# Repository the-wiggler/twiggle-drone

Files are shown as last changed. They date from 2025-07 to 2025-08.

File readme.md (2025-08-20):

## Twiggle Drone Project
An from-scratch quadcopter built using Arduino, and capable of stable flight controlled via a WiFi connection. 

---

## Features
- Built with **Arduino Nano ESP32**
- 4x Brushless motors with PWM control
- ICM20948 for attitude sensing
- Custom PID stabilization program
- Manual flight via a GUI computer program (UDP over WiFi)

## Components
| Component | Description | Quantity | Link |
|---|---|---|---|
| Arduino Nano ESP32 | Main microcontroller | 1 | [Link](https://www.digikey.com/en/products/detail/arduino/ABX00092/21219771) |
| Adafruit ICM20948 | Gyroscope + Accelerometer | 1 | [Link](https://www.digikey.com/en/products/detail/adafruit-industries-llc/4554/17039173) |
| Adafruit Powerboost 1000 | 3.7V → 5V power converter | 1 | [Link](https://www.digikey.com/en/products/detail/adafruit-industries-llc/2030/5011076) |
| Adafruit USB C Breakout | Provide power to Arduino USB C port | 1 | [Link](https://www.digikey.com/en/products/detail/adafruit-industries-llc/5978/24639123) |
| N-Channel MOSFET | Used for PWM motor control | 4 | [Link](https://www.digikey.com/en/products/detail/infineon-technologies/IRLZ44NPBF/811808) |
| 8520 Coreless Brushed Motors | Drone motors/rotors | 4 | [Link](https://www.amazon.com/dp/B076M7G24G?ref=ppx_yo2ov_dt_b_fed_asin_title) |
| GNB 3.8V 520mAh LiPo Battery (80C) | Battery | 1 | [Link](https://www.amazon.com/dp/B07QC17GLT?ref=ppx_yo2ov_dt_b_fed_asin_title) |
| Drone Body | 3D printed body | 1 | [link](about:blank) |

## Project Structure
twiggle-drone/<br>
├── src/<br>
│   ├── main.cpp<br>
│   └── // arduino files (to be uploaded to arduino)<br>
├── controller/<br>
│   ├── main.cpp<br>
│   └── // controller files (to be run on local machine)<br>

## Getting Started
1. **Construct the drone**
    - The drone is activated when it receives battery power, and will wait for controller input via UDP over wifi
2. **Run the controller program**
    - build the controller program found in /controller/
    - this program should be run on a computer with the ability to connect to WiFi networks
    - connect to the drone's WiFi network before running the program
    - run the program, and the drones motors should begin at an idle state. The drone is ready to fly
### Schematic:
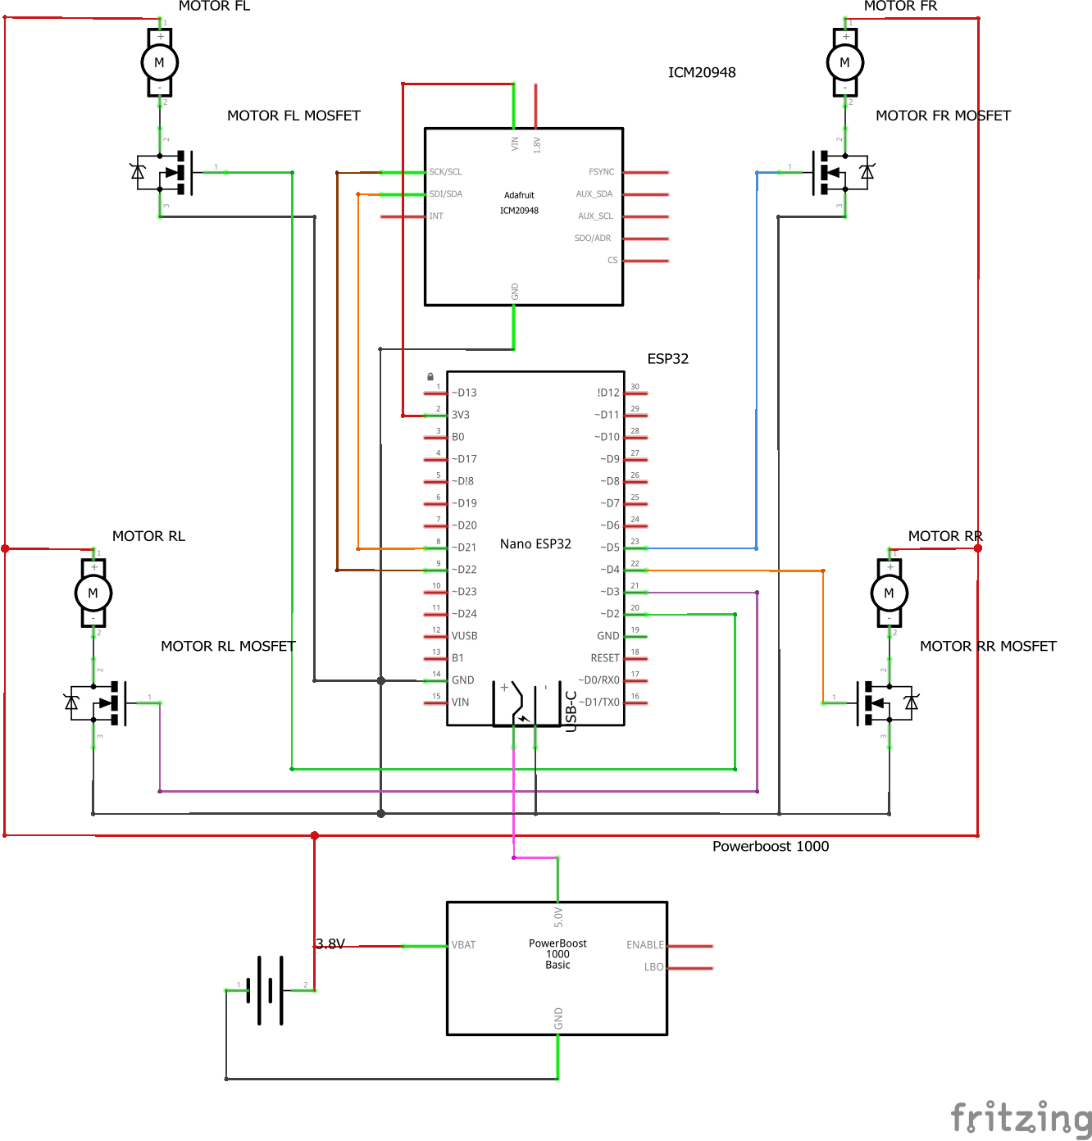
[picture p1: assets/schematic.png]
schematic


## Building the Firmware
1. Install [Arduino IDE](https://www.arduino.cc/en/software) or use PlatformIO
2. Install support for **Arduino Nano ESP32**
3. Clone this repo
4. Open `src/main.cpp` in the IDE and upload to the board

## Building the Controller (PC-side)
1. Requires C++17, SDL3
2. Run the build script

## Building the Drone Body
1. Download the STL files found in the assets folder
2. Recommended 3d print settings: PLA, 100% infill
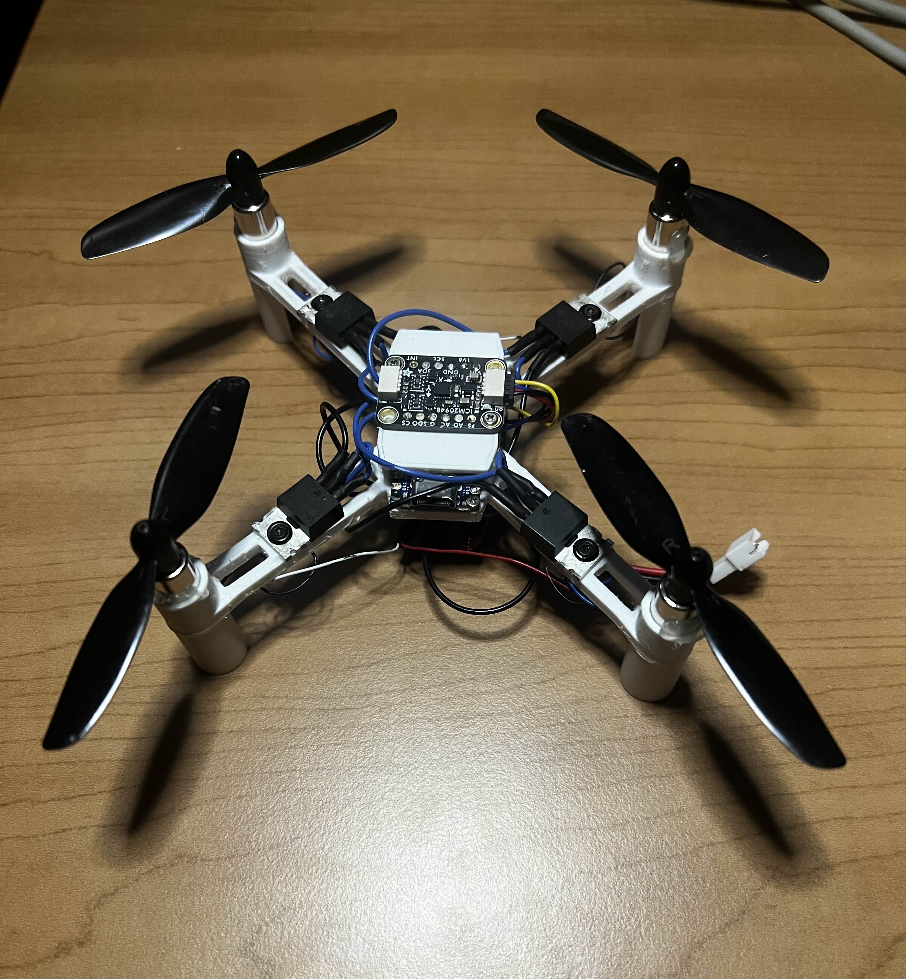
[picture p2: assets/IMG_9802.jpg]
drone_body_pic


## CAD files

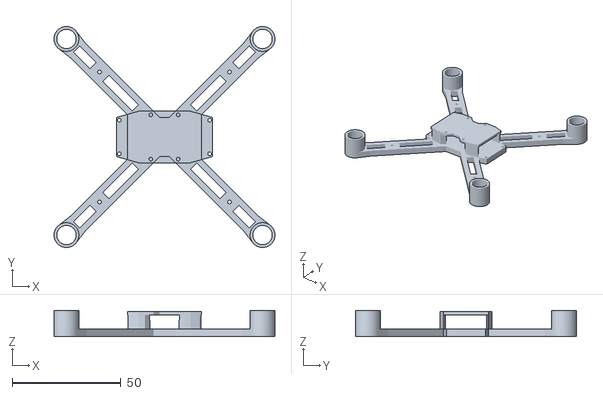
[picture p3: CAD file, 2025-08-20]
assets/drone_body.stl
101.4 x 101.4 x 12.0

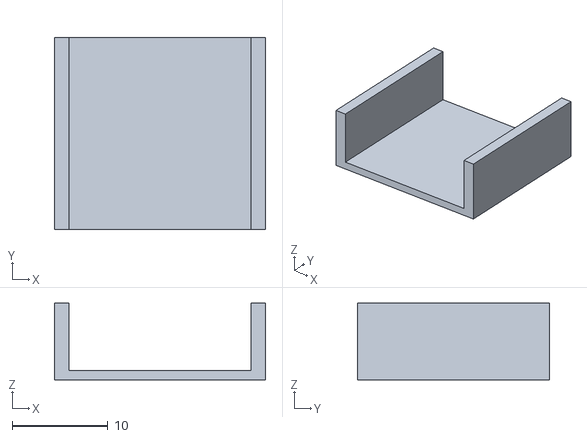
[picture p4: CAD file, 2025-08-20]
assets/battery_holder.stl
22.0 x 20.0 x 8.00

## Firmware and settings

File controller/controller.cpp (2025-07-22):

#include <iostream>
#include <string>
#include <sstream>
#include <winsock2.h>
#include <ws2tcpip.h>
#include <SDL3/SDL.h>
#include <SDL3_ttf/SDL_ttf.h>
#include "controller.hpp"
#include <cmath>
#include <chrono>
#include <thread>
#include <iomanip>
#pragma comment(lib, "ws2_32.lib")

TTF_Font* font = nullptr;

// hi there if you're reading this :)
// im sorry because this controller program is very poorly formatted im just kind of throwing it together
// good luck!

////////////////////////////////////////////////////////////////////////////////////////////////////
// MAIN
////////////////////////////////////////////////////////////////////////////////////////////////////

int main() {
    /////// SETUP //////////////////////////////////////////////////////////////////////////////
    // SDL
    SDL_Init(SDL_INIT_VIDEO);
    TTF_Init();
    SDL_SetRenderDrawBlendMode(renderer, SDL_BLENDMODE_BLEND);
    std::string fontPath = SDL_GetBasePath();
    fontPath += "font.ttf";
    font = TTF_OpenFont(fontPath.c_str(), 24);
    if (!font) SDL_ShowSimpleMessageBox(0x00000010, "Drone Controller", 
                                        "ERROR: FONT FILE <font.ttf> NOT FOUND", NULL);
    constexpr SDL_Color whiteColor = {255, 255, 255, 255};
    
    // UDP Communication
    WSADATA wsaData;
    WSAStartup(MAKEWORD(2, 2), &wsaData);
    
    SOCKET sock = socket(AF_INET, SOCK_DGRAM, IPPROTO_UDP);
    sockaddr_in addr = {AF_INET, htons(8888)};
    inet_pton(AF_INET, "192.168.4.1", &addr.sin_addr);

    // drone setup
    float throttlePercent = 0.0f;
    
    // Clickable parameter boxes
    float proportional = 50.0f;
    float integral = 0.0f;
    float derivative = 0.0f;

    ///////////////////////////////////////////////////////////////////////  /  /  /  /  /  ///////
    /////// MAIN WINDOW LOOP                                        ////////////////////////////////
    ///////////////////////////////////////////////////////////////////////  /  /  /  /  /  ///////
    bool windowRunning = true;
    bool motorsKilled = false;
    bool pidTuning = false; // set to true if you want to modify PID data via UDP (dangerous)
    SDL_Event e;

    float throttleLevel = 0.0f;

    while (windowRunning) {
        bool boxClicked = false;
        
        SDL_SetRenderDrawColor(renderer, 37,37,37,255);
        SDL_RenderClear(renderer);
        setControlOutline();

        // get window size for positioning the red box
        int windowWidth, windowHeight;
        SDL_GetWindowSize(window, &windowWidth, &windowHeight);
        float redBoxX = windowWidth - RED_BOX_SIZE - RED_BOX_MARGIN;
        float redBoxY = windowHeight - RED_BOX_SIZE - RED_BOX_MARGIN;

        // render red box for PID tuning toggle
        SDL_SetRenderDrawColor(renderer, 255, 0, 0, 255);
        SDL_FRect redBox = {redBoxX, redBoxY, RED_BOX_SIZE, RED_BOX_SIZE};
        SDL_RenderFillRect(renderer, &redBox);

        // if the red box is clicked do all the things
        if (pidTuning) renderParameterBoxes(proportional, integral, derivative, font, renderer);

        // check for any SDL window events
        while  (SDL_PollEvent(&e)) {
            if (e.type == SDL_EVENT_QUIT) {
                windowRunning = false;
            }
            else if (e.type == SDL_EVENT_MOUSE_BUTTON_DOWN) {
                if (e.button.button == SDL_BUTTON_LEFT) {
                    float mouseX = e.button.x;
                    float mouseY = e.button.y;

                    // check if red box was clicked
                    if (mouseX >= redBoxX && mouseX <= redBoxX + RED_BOX_SIZE &&
                        mouseY >= redBoxY && mouseY <= redBoxY + RED_BOX_SIZE) {
                        pidTuning = true;
                        std::cout << "PID Tuning enabled" << std::endl;
                    }

                    for (int i = 0; i < 3; i++) {
                        float boxX = BOX_START_X + i * (BOX_WIDTH + BOX_SPACING);
                        float boxY = BOX_START_Y;
                        if (pidTuning) {
                            if (mouseX >= boxX && mouseX <= boxX + BOX_WIDTH &&
                                mouseY >= boxY && mouseY <= boxY + BOX_HEIGHT) {
                                if (i == 0) proportional += 10;
                                else if (i == 1) integral += 5;
                                else if (i == 2) derivative += 1;
                                boxClicked = true;
                            }
                        }
                    }
                }
                if (e.button.button == SDL_BUTTON_RIGHT) {
                    float mouseX = e.button.x;
                    float mouseY = e.button.y;

                    for (int i = 0; i < 3; i++) {
                        float boxX = BOX_START_X + i * (BOX_WIDTH + BOX_SPACING);
                        float boxY = BOX_START_Y;
                        if (pidTuning) {
                            if (mouseX >= boxX && mouseX <= boxX + BOX_WIDTH &&
                                mouseY >= boxY && mouseY <= boxY + BOX_HEIGHT) {
                                if (i == 0) proportional -= 10;
                                else if (i == 1) integral -= 5;
                                else if (i == 2) derivative -= 1;
                                boxClicked = true;
                        }
                        }
                    }
                }
            }
        }

        // these are the components of the direction vector instruction to be converted into setpoint measurements
        // (in radians) that will be sent to the drone
        controlVector controlVectors;
        controlVectors.roll = 0;
        controlVectors.pitch = 0;
        controlVectors.yaw = 0;

        const bool* keyStates = SDL_GetKeyboardState(NULL);
        bool w_pressed = keyStates[SDL_SCANCODE_W]; // if the w key is pressed
        bool s_pressed = keyStates[SDL_SCANCODE_S];
        bool a_pressed = keyStates[SDL_SCANCODE_A];
        bool d_pressed = keyStates[SDL_SCANCODE_D];
        bool q_pressed = keyStates[SDL_SCANCODE_Q];
        bool e_pressed = keyStates[SDL_SCANCODE_E];
        bool space_pressed = keyStates[SDL_SCANCODE_SPACE];
        bool shift_pressed = keyStates[SDL_SCANCODE_LSHIFT];
        bool control_pressed = keyStates[SDL_SCANCODE_LCTRL];
        bool esc_pressed = keyStates[SDL_SCANCODE_ESCAPE];
        bool zero_pressed = keyStates[SDL_SCANCODE_0];

        if (w_pressed && !s_pressed) {
            controlVectors.pitch = 127; // set a control vector component to FORWARD direction
            moveForward();
        }
        if (s_pressed && !w_pressed) {
            controlVectors.pitch = -127; // set a control vector component to BACKWARD direction
            moveBackward();
        }
        if (a_pressed && !d_pressed) { 
            controlVectors.roll = -127; // set a control vector component to LEFT direction
            moveLeft(); 
        }
        if (d_pressed && !a_pressed) {
            controlVectors.roll = 127; // set a control vector component to RIGHT direction
            moveRight();
        }
        if (q_pressed && !e_pressed) {
            controlVectors.yaw = -127;
            yawLeft();
        }
        if (e_pressed && !q_pressed) {
            controlVectors.yaw = 127;
            yawRight();
        }
        if (shift_pressed) {
            if (throttleLevel < 100.0f) throttleLevel += 1.0f;
            if (throttleLevel > 100.0f) throttleLevel = 100.0f;
        }
        if (control_pressed) {
            if (throttleLevel > 0.0f) throttleLevel -= 1.0f;
            if (throttleLevel < 0.0f) throttleLevel = 0.0f;
        }
        if (esc_pressed) windowRunning = false;
        if (zero_pressed) {
            throttleLevel = 0.0f;
            std::cout << "MOTORS KILLED!\n";
            motorsKilled = true;
        }

        /////// CONVERT VECTORS TO SETPOINTS ///////////////////////////////////////////////////////
        // these are the new setpoint values that should be sent to the drone after recieving controller input
        float rollSetpoint = convertVectorToSetpoint(controlVectors.roll);
        float pitchSetpoint = convertVectorToSetpoint(controlVectors.pitch);
        float yawSetpoint = convertVectorToSetpoint(controlVectors.yaw);

        /////// SEND UDP DATA //////////////////////////////////////////////////////////////////////
        // udp_data is an array that holds all control data to be sent to the drone. The drone
        // will recognize the bytes in a set format defined below, so it must match on both programs!
        // the first element is what to change the throttle to
        // the second and third element is what vector the drone should aim to change its direction of travel to

        udpPacket packet = { 'c', percentageToThrottle(throttleLevel), rollSetpoint, pitchSetpoint, yawSetpoint };
        int len = sizeof(packet);
        sendto(sock, (const char*)&packet, len, 0, (sockaddr*)&addr, sizeof(addr));

        if (boxClicked && pidTuning) {
            udpPacket pidPacket = { 'p', 0, proportional, integral, derivative };
            int pidlen = sizeof(pidPacket);
            sendto(sock, (const char*)&pidPacket, pidlen, 0, (sockaddr*)&addr, sizeof(addr));
            std::cout << "PACKET CONTENTS: "
                << pidPacket.identifier
                << " " << pidPacket.throttle 
                << " " << pidPacket.roll
                << " " << pidPacket.pitch 
                << " " << pidPacket.yaw
                << std::dec << std::endl;
        }

        std::cout << "PACKET CONTENTS: "
            << packet.identifier
            << " " << packet.throttle 
            << " " << packet.roll
            << " " << packet.pitch 
            << " " << packet.yaw
            << std::dec << std::endl;  // Reset to decimal

        /////// THROTTLE TEXT //////////////////////////////////////////////////////////////////////
        std::stringstream throttleStream;
        throttleStream << "Throttle: " << std::fixed << std::setprecision(1) << throttleLevel << "%";
        std::string throttleText = throttleStream.str();
        SDL_Surface* throttleSurface = TTF_RenderText_Blended(font, throttleText.c_str(), throttleText.length(), whiteColor);
        SDL_Texture* throttleTexture = SDL_CreateTextureFromSurface(renderer, throttleSurface);
        SDL_FRect textRect = {50.0f, 50.0f, (float)throttleSurface->w, (float)throttleSurface->h};
        
        SDL_RenderTexture(renderer, throttleTexture, NULL, &textRect);
        SDL_DestroyTexture(throttleTexture);  // Clean up texture
        SDL_DestroySurface(throttleSurface);  // Clean up surface

        /////// TEXT //////////////////////////////////////////////////////////////////////

        /////// TEXT //////////////////////////////////////////////////////////////////////
        
        SDL_RenderPresent(renderer);
        SDL_Delay(32);

        if (motorsKilled) {
            windowRunning = false;
            std::this_thread::sleep_for(std::chrono::seconds(2));
        }
    }

    /////// CLEANUP ////////////////////////////////////////////////////////////////////////////////
    TTF_CloseFont(font);
    SDL_DestroyRenderer(renderer);
    SDL_DestroyWindow(window);
    TTF_Quit();
    SDL_Quit();
    closesocket(sock);
    WSACleanup();

    return 0;
}

////////////////////////////////////////////////////////////////////////////////////////////////////
// END MAIN
////////////////////////////////////////////////////////////////////////////////////////////////////

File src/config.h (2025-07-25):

#ifndef CONFIG_H
#define CONFIG_H

#include <Arduino.h>

constexpr uint8_t MOTOR_FL_PIN 		= 3; 	// pin for motor front left
constexpr uint8_t MOTOR_FR_PIN 		= 2; 	// pin for motor front right
constexpr uint8_t MOTOR_RL_PIN 		= 4; 	// pin for motor rear left
constexpr uint8_t MOTOR_RR_PIN 		= 5; 	// pin for motor rear right

constexpr uint8_t MOTOR_FL 			= 0; 	// PWM channel for motor front left
constexpr uint8_t MOTOR_FR 			= 1; 	// PWM channel for motor front right
constexpr uint8_t MOTOR_RL 			= 2;	// PWM channel for motor rear left
constexpr uint8_t MOTOR_RR 			= 3; 	// PWM channel for motor rear right

constexpr uint32_t PWM_FREQUENCY 	= 15000;	// PWM update frequency
constexpr uint8_t  PWM_RESOLUTION 	= 10;	// PWM resolution (bits)

extern bool SYSTEM_FAILURE;

#endif

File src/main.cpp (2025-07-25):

#include <Arduino.h>
#include <Adafruit_ICM20X.h>
#include <Adafruit_ICM20948.h>
#include <Adafruit_Sensor.h>
#include <Wire.h>

#include "config.h"
#include "motors.h"
#include "sensors.h"
#include "PID.h"
#include "debug.h"
#include "communication.h"

SemaphoreHandle_t controlPacketMutex;
SemaphoreHandle_t pidPacketMutex;

// buffers for control packets
udpPacket controlPacketBuffer[2];
volatile int activeBuffer = 0;
volatile int writeBuffer = 1;

// packet timeout
unsigned long lastPacketTime = 0;
const unsigned long PACKET_TIMEOUT_MS = 2000; // 2 second timeout
bool packetTimeout = false;

////////////////////////////////////////////////////////////////////////////////////////////////////
// SETUP
////////////////////////////////////////////////////////////////////////////////////////////////////
void core0Process(void *parameter);

void setup() {
	Serial.begin(115200);

	// potential fix to motors running a small amount when the battery gives initial power
	digitalWrite(MOTOR_FL_PIN, LOW);
	digitalWrite(MOTOR_FR_PIN, LOW);
	digitalWrite(MOTOR_RL_PIN, LOW);
	digitalWrite(MOTOR_RR_PIN, LOW);

	delay(3000); // small delay to allow serial monitor to set up

	// initialize mutexes for core 0 & 1 shared variables
	controlPacketMutex 	= xSemaphoreCreateMutex();
	pidPacketMutex 		= xSemaphoreCreateMutex();

	// sets initial default value to control packet buffers
	controlPacketBuffer[0] = {0, 0, 0, 0};
	controlPacketBuffer[1] = {0, 0, 0, 0};

	lastPacketTime = millis();
	packetTimeout = false;

	wifiSetup();

	initializeMotors();
	initializeSensors();

	/////// CORE TASK SETUP ////////////////////////////////////////////////////////////////////////
	xTaskCreatePinnedToCore(
		core0Process,
		"core0Process",
		20000,
		NULL,
		2,
		NULL,
		0
	);
	////////////////////////////////////////////////////////////////////////////////////////////////
	
	// wait
	Serial.println("Startup...");
	delay(1000);

	initializePID();
}
////////////////////////////////////////////////////////////////////////////////////////////////////
// END SETUP
////////////////////////////////////////////////////////////////////////////////////////////////////


////////////////////////////////////////////////////////////////////////////////////////////////////
// CORE 1 LOOP
////////////////////////////////////////////////////////////////////////////////////////////////////
bool SYSTEM_FAILURE = false;
constexpr unsigned long LOOP_INTERVAL = 5000; // 5ms is a 200 Hz delay for the PID system

// this is a variable that core 0 writes to when it recieves a packet
// core 1 uses setpoint data from this packet to make adjustments to the drone orientation via the
// PID functions
udpPacket control_packet;
udpPacket pid_packet;

void loop() {
	if (SYSTEM_FAILURE) return;
	
	// checks if a packet has been received from the controller recently, if not, it kills motors
	//if (checkPacketTimeout(lastPacketTime, PACKET_TIMEOUT_MS, packetTimeout)) return;
	// restores motor control if a packet has been received 
	if (packetTimeout) packetTimeout = false;

	// this collects info from control_packet so its memory safe

	udpPacket localControlPacket;
	// read of control_packet
	if (xSemaphoreTake(controlPacketMutex, 0)) {	// 0 means dont wait if its taken
		localControlPacket = controlPacketBuffer[activeBuffer];
		xSemaphoreGive(controlPacketMutex); // release packet mutex
	}

	unsigned long  startTime = micros();	

	// reads the gyroscope data and writes it to sensor arrays
	readICM();

	// calculates the orientation of the drone (in radians) based off of stored sensor data
	calculateOrientation();

	// calculate PID outputs if the sensor data is safe to access (not being used)
	PIDControl(localControlPacket.roll, localControlPacket.pitch, localControlPacket.yaw, 
				400);

	// sends the new motor speeds to the PWM hardware
	updateMotorSpeed();

	// debug stuff
	//monitorRollPitchPID(rollOutput, pitchOutput, yawOutput);
	monitorMotorSpeeds();
	//logData(rollOutput, pitchOutput);

	// maintains the 200 Hz clock speed
	unsigned long elapsedTime = micros() - startTime;
	if (elapsedTime < LOOP_INTERVAL) delayMicroseconds(LOOP_INTERVAL - elapsedTime); 
}
////////////////////////////////////////////////////////////////////////////////////////////////////
// END CORE 1
////////////////////////////////////////////////////////////////////////////////////////////////////

////////////////////////////////////////////////////////////////////////////////////////////////////
// CORE 0 LOOP
////////////////////////////////////////////////////////////////////////////////////////////////////
void core0Process(void *parameter) {
	while(true) {
		if (!SYSTEM_FAILURE) {
			udpPacket receivedPacket;

			// only updates control_packet if a new packet was received
			if (receiveUDPCommand(receivedPacket) && receivedPacket.identifier == 'c') {
				controlPacketBuffer[writeBuffer] = receivedPacket;

				// responsible for keeping track of connection status
				lastPacketTime = millis();
				packetTimeout = false;

				// if available, writes newly recieved packet to global control_packet variable
				if (xSemaphoreTake(controlPacketMutex, 3 / portTICK_PERIOD_MS)) {
					int temp = activeBuffer;
					activeBuffer = writeBuffer;
					writeBuffer = temp;
					xSemaphoreGive(controlPacketMutex);
				}
				// if the mutex cant be written to, the new packet will be used next time!
			}
			else if (receivedPacket.identifier == 'p') {
				if(xSemaphoreTake(pidPacketMutex, 3 / portTICK_PERIOD_MS)) {
					pid_packet = receivedPacket;
					xSemaphoreGive(pidPacketMutex);
				}
			}
		}
		vTaskDelay(10 / portTICK_PERIOD_MS); 
	}
}
////////////////////////////////////////////////////////////////////////////////////////////////////
// END CORE 0
////////////////////////////////////////////////////////////////////////////////////////////////////

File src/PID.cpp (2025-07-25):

#include <Arduino.h>
#include "config.h"
#include "sensors.h"
#include "motors.h"
#include "PID.h"
#include <cmath>

////////////////////////////////////////////////////////////////////////////////////////////////////
// PID FUNCTIONS
////////////////////////////////////////////////////////////////////////////////////////////////////

// PID Coefficients (change for tuning)
PID ROLL_ATTITUDE_PID	{ 200.0, 0.0, 0.0 };
PID PITCH_ATTITUDE_PID	{ 200.0, 0.0, 0.0 };
PID YAW_ATTITUDE_PID	{ 10.0, 0.0, 0.0 };

PID ROLL_RATE_PID		{ 10.0, 0.0, 0.0 };
PID PITCH_RATE_PID		{ 10.0, 0.0, 0.0 };
PID YAW_RATE_PID		{ 05.0, 0.0, 0.0 };

// stores error states of an iteration so the program can bring the state closer to setpoints
PIDErrors rollAttitudeErrors	{ 0, 0, 0, 0 };
PIDErrors pitchAttitudeErrors	{ 0, 0, 0, 0 };
PIDErrors yawAttitudeErrors		{ 0, 0, 0, 0 };

PIDErrors rollRateErrors		{ 0, 0, 0, 0 };
PIDErrors pitchRateErrors		{ 0, 0, 0, 0 };
PIDErrors yawRateErrors			{ 0, 0, 0, 0 };

float MAX_ROLL_RATE 	= 0.3;
float MAX_PITCH_RATE 	= 0.3;
float MAX_YAW_RATE 		= 0.15;

constexpr float ATTITUDE_INTEGRAL_MAX = 5;
constexpr float ATTITUDE_INTEGRAL_MIN = 5;
constexpr float RATE_INTEGRAL_MAX = 20.0;
constexpr float RATE_INTEGRAL_MIN = -20.0;

void resetPID() {

}

float calculatePID(const PID& pidCoeffs, PIDErrors& errors, float setpoint, float currentState) {
	unsigned long currentTime = micros();
	// convert time from ms to seconds
	float deltaTime = (currentTime - errors.lastTime) / 1000000.0;
	
	// calculate current error
	errors.currentError = setpoint - currentState;

	if ((errors.currentError > 0) != (errors.previousError > 0)) errors.integral = 0;

	// calcualte integral
	errors.integral += errors.currentError * deltaTime;

	// calculate derivative
	float derivative = 0;
	if (deltaTime > 0) {
		derivative = (errors.currentError - errors.previousError) / deltaTime;
	}

	// calculate PID output
	float output = 	(pidCoeffs.Kp * errors.currentError) + 
					(pidCoeffs.Ki * errors.integral) +
					(pidCoeffs.Kd * derivative);

	// update for next iteration
	errors.previousError = errors.currentError;
	errors.lastTime = currentTime;

	return output;
}

void updateMotorsFromPID(float rollOutput, float pitchOutput, float yawOutput, uint32_t throttle) {
	float speedFL = throttle + pitchOutput + rollOutput + yawOutput;
	float speedFR = throttle + pitchOutput - rollOutput - yawOutput;
	float speedRL = throttle - pitchOutput + rollOutput + yawOutput;
	float speedRR = throttle - pitchOutput - rollOutput - yawOutput;

	motorSpeed[MOTOR_FL] = constrain(speedFL, 0, 1023);
	motorSpeed[MOTOR_FR] = constrain(speedFR, 0, 1023);
	motorSpeed[MOTOR_RL] = constrain(speedRL, 0, 1023);
	motorSpeed[MOTOR_RR] = constrain(speedRR, 0, 1023);
}

void PIDControl(float desiredRoll, float desiredPitch, float desiredYaw, uint32_t throttle) {
	// attitude control (reads the angle and turns it into a desired turn rate)
	float desiredRollRate 	= calculatePID(ROLL_ATTITUDE_PID, rollAttitudeErrors, 
										 	desiredRoll, orientations.roll);
	float desiredPitchRate 	= calculatePID(PITCH_ATTITUDE_PID, pitchAttitudeErrors, 
										  	desiredPitch, orientations.pitch);
	float desiredYawRate 	= calculatePID(YAW_ATTITUDE_PID, yawAttitudeErrors, 
											desiredYaw, orientations.yaw);
	
	// constrains rates to the max limits allowed by the controller
	desiredRollRate 	= constrain(desiredRollRate, -MAX_ROLL_RATE, MAX_ROLL_RATE);
	desiredPitchRate 	= constrain(desiredPitchRate, -MAX_PITCH_RATE, MAX_PITCH_RATE);
	desiredYawRate 		= constrain(desiredYawRate, -MAX_YAW_RATE, MAX_YAW_RATE);

	// rate control (reads the desited turn rate and transforms it into appropriate motor outputs)
	float rollOutput 	= calculatePID(ROLL_RATE_PID, rollRateErrors, 
										desiredRollRate, angularV.roll);
	float pitchOutput 	= calculatePID(PITCH_RATE_PID, pitchRateErrors, 
										desiredPitchRate, angularV.pitch);
	float yawOutput 	= calculatePID(YAW_RATE_PID, yawRateErrors, 
										desiredYawRate, angularV.yaw);
	
	updateMotorsFromPID(rollOutput, pitchOutput, yawOutput, throttle);
}

void initializePID() {
    unsigned long currentTime = micros();
    rollAttitudeErrors.lastTime = currentTime;
    pitchAttitudeErrors.lastTime = currentTime;
    yawAttitudeErrors.lastTime = currentTime;
	rollRateErrors.lastTime = currentTime;
    pitchRateErrors.lastTime = currentTime;
    yawRateErrors.lastTime = currentTime;
}

////////////////////////////////////////////////////////////////////////////////////////////////////
// END PID FUNCTIONS
////////////////////////////////////////////////////////////////////////////////////////////////////

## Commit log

2025-06-22 added more defined motor control functions
2025-06-22 added PID and sensor control
2025-06-22 motor PID control update
2025-06-22 PID calibration improvement
2025-06-26 fixed for current drone application
    [main.cpp]
2025-06-26 updated the core structure
    all non-PID and motor correction tasks will run on core 0 from now on so the motors can update at a constant 200 Hz
    [main.cpp]
2025-07-08 created UDP communication feature and software controller
    right now the controller only sends packets of information over UDP to the controller, which prints it to the serial terminal. neither the controller or the arduino communication program actually DO 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
2025-07-09 successfully implemented vector and throttle data transmission via UDP
2025-07-10 implemented wireless motor control
    the controller now sends packets of data that effectively control the setpoints that are entered into the PID calculations, meaning that when a direction instruction is sent to the drone, it will adj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
2025-07-10 packet timeout and more reliable motor control
    made it so the motors cut power if a control packet hasnt been received in 2 seconds. Additionally packets now write to a buffer now so the mutex isnt always being held by core 0 (this resulted in un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
2025-07-11 made adjustments to PID coefficients. Increased stability
    [PID.cpp, datalogger.py]
2025-07-15 ! restructured cpp and h files
    I did not test this on the drone but it compiles without errors. Hopefully it doesnt break things! :)
    [PID.cpp, main.cpp, motors.cpp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]
2025-07-17 added schematic
    [Schematic.fzz]
2025-07-17 changed folder name
    [Schematic.fzz]
2025-07-18 migrated sensor reading from core 0 to core 1
2025-07-19 added fix that prevents random crashing
    [PID.cpp, main.cpp]
2025-07-19 added ability to control PID values from the controller
    by pressing the red square
2025-07-21 temp - does not work right
    [PID.cpp, controller.cpp, controller.hpp]
2025-07-21 overhauled the throttle system to use more precise logic
    [drone_data.csv]
2025-07-21 adjusted PWM_FREQUENCY 10 15khz
2025-07-22 added yaw PID and motor tuning
    [drone_data.csv]
2025-07-22 added yaw control to the controller
2025-07-22 added cascaded PID system that MIGHT work?
2025-07-25 edited some PID stuff
2025-08-20 added drone body STL files
    [battery_holder.stl, drone_body.stl]
